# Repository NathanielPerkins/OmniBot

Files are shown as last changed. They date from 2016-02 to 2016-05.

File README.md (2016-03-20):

# OmniBot
EESS Modular Robotics Platform
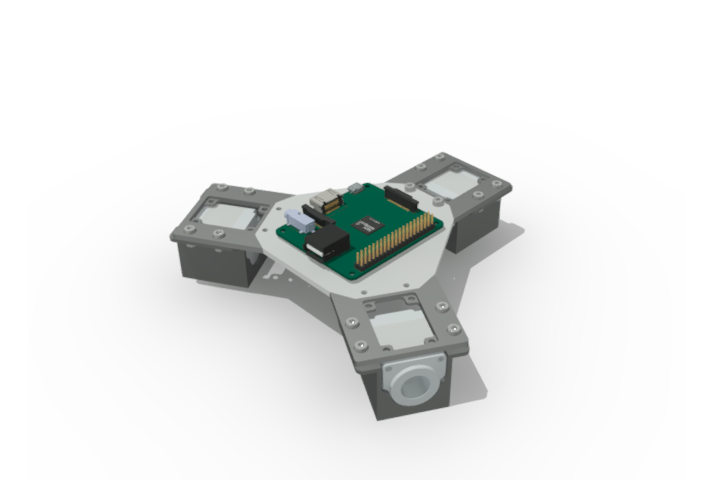
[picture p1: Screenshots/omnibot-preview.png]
OmniBot Render


An open source modular robotics platform designed with KiCAD and FreeCAD.
Custom designed Chassis designed to be laser cut/3d printed/CnC Milled. Custom fit stepper motor mounts with embedded motor controller PCB.

Main Processor unit consists of a Raspberry Pi A+ for path planning and general computation. An STM32 ARM microcontroller system controller will handle the stepper motor control via communication with the RPi A+ board and motor controllers. 

1: System Controller

Requirements: The Electronics design require the following footprint libraries for KiCAD

https://github.com/NathanielPerkins/NPFootprints.pretty
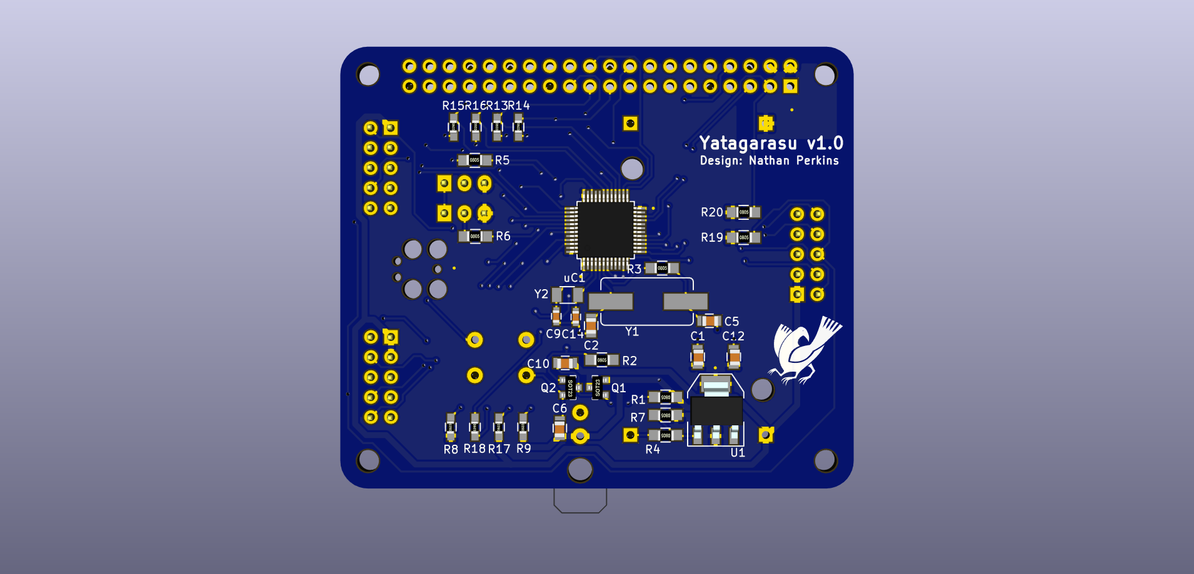
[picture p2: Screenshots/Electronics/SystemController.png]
System Controller


2: Mechanical

Chassis design for overall OmniBot frame, and motor mount system

3: Motor Controller

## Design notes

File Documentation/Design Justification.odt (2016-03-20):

# OmniBot Design Justification

## Electrical

### Component Selection

### Decoupling

All decoupling capacitors are the standard values given in the STM32F10xx hardware design document.

### Programming/Debugging

Pin-outs were selected for the SWD interface based on the STLink/V2 and third party Tag-Connect connector and cable.

### Boot Mode

Jumpers to select boot mode were selected due to cost and simplicity of use. 10K Resistors were selected from the STM32F10xx Hardware Design datasheet recommendations. BOOT0 has no further functionality, however BOOT1 can be used as a general I/O.

### External Power Controller

Design was based off similar purpose IC chips linked below, capacitor (1nF) was estimated based on IC chip solutions.

http://www.vishay.com/docs/73449/si1869dh.pdf

http://www.onsemi.com/pub_link/Collateral/AND9093-D.PDF

### Crystal

Crystal capacitance values were calculated using formulae derived from the following links.

Stray capacitance, from the STM32F103CBT6 datasheet lists the pin capacitance as 5pF. A further 2pF was estimated due to track considerations and a 20pF crystal was used for calculations regarding the High Speed External Clock.

http://www.seeedstudio.com/depot/images/opl/datasheet/306010033.pdf

http://ww1.microchip.com/downloads/en/AppNotes/00826a.pdf

Rs = 910ohms was calculated with the following link

http://www.crystek.com/documents/appnotes/Pierce-GateIntroduction.pdf

### USB

USB 2.0 High speed was selected over USB OTG primarily due to added cost of OTG with no added benefit for current application.

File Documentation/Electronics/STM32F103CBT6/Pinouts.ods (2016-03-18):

Pin | Name | Type | Features |  |  | After Reset | Alternate (default) |  |  |  |  | Alternate (Remap) |  |  | 5V Tolerant | Notes
1 | V_Bat | S |  |  |  |  |  |  |  |  |  |  |  |  | No
2 | PC13-Tamper-RTC | I/O |  |  |  | PC13 | Tamper-RTC |  |  |  |  |  |  |  | No
3 | PC14-OSC32_IN | I/O | Clock |  |  | PC14 | OSC32_IN |  |  |  |  |  |  |  | No
4 | PC15-OSC32_OUT | I/O | Clock |  |  | PC15 | OSC32_OUT |  |  |  |  |  |  |  | No
5 | OSC_IN | I | Clock |  |  | OSC_IN |  |  |  |  |  | PD0 |  |  | No | PD0 output only in 50mHz mode
6 | OSC_OUT | O | Clock |  |  | OSC_OUT |  |  |  |  |  | PD1 |  |  | No | PD1 output only in 50mHz mode
7 | NRST | I/O | JTAG |  |  | NRST |  |  |  |  |  |  |  |  | No
8 | V_SSA | S |  |  |  | V_SSA |  |  |  |  |  |  |  |  | No
9 | V_DDA | S |  |  |  | V_DDA |  |  |  |  |  |  |  |  | No
10 | PA0-WKUP | I/O | Communication | ADC | Timer | PA0 | USART2_CTS | ADC12_IN0 | TIM2_CH1_ETR |  | Wakeup |  |  |  | No
11 | PA1 | I/O | Communication | ADC | Timer | PA1 | USART2_RTS | ADC12_IN1 | TIM2_CH2 |  |  |  |  |  | No
12 | PA2 | I/O | Communication | ADC | Timer | PA2 | USART2_TX | ADC12_IN2 | TIM2_CH3 |  |  |  |  |  | No
13 | PA3 | I/O | Communication | ADC | Timer | PA3 | USART2_RX | ADC12_IN3 | TIM2_CH4 |  |  |  |  |  | No
14 | PA4 | I/O | Communication | ADC |  | PA4 | USART2_CK | ADC12_IN4 |  |  | SPI1_NSS |  |  |  | No
15 | PA5 | I/O | Communication | ADC |  | PA5 |  | ADC12_IN5 |  |  | SPI1_SCK |  |  |  | No
16 | PA6 | I/O | Communication | ADC | Timer | PA6 |  | ADC12_IN6 | TIM3_CH1 |  | SPI1_MISO |  | TIM1_BKIN |  | No
17 | PA7 | I/O | Communication | ADC | Timer | PA7 |  | ADC12_IN7 | TIM3_CH2 |  | SPI1_MOSI |  | TIM1_CH1 |  | No
18 | PB0 | I/O | Communication | ADC | Timer | PB0 |  | ADC12_IN8 | TIM3_CH3 |  |  |  | TIM1_CH2 |  | No
19 | PB1 | I/O | Communication | ADC | Timer | PB1 |  | ADC12_IN9 | TIM3_CH4 |  |  |  | TIM1_CH3 |  | No
20 | PB2 | I/O |  |  |  | PB2/BOOT1 |  |  |  |  |  |  |  |  | Yes
21 | PB10 | I/O | Communication |  | Timer | PB10 | USART3_TX |  |  | I2C2_SCL |  |  | TIM2_CH3 |  | Yes
22 | PB11 | I/O | Communication |  | Timer | PB11 | USART3_RX |  |  | I2C2_SDA |  |  | TIM2_CH4 |  | Yes
23 | V_SS1 | S |  |  |  | V_SS1 |  |  |  |  |  |  |  |  | No
24 | V_DD1 | S |  |  |  | V_DD1 |  |  |  |  |  |  |  |  | No
25 | PB12 | I/O | Communication |  | Timer | PB12 | USART3_CK |  | TIM1_BKIN |  | SPI2_NSS |  |  |  | Yes
26 | PB13 | I/O | Communication |  | Timer | PB13 | USART3_CTS |  | TIM1_CH1N |  | SPI2_SCK |  |  |  | Yes
27 | PB14 | I/O | Communication |  | Timer | PB14 | USART3_RTS |  | TIM1_CH2N |  | SPI2_MISO |  |  |  | Yes
28 | PB15 | I/O | Communication |  | Timer | PB15 |  |  | TIM1_CH3N |  | SPI2_MOSI |  |  |  | Yes
29 | PA8 | I/O | Communication |  | Timer | PA8 | USART1_CK |  | TIM1_CH1 |  | MCO |  |  |  | Yes
30 | PA9 | I/O | Communication |  | Timer | PA9 | USART1_TX |  | TIM1_CH2 |  |  |  |  |  | Yes
31 | PA10 | I/O | Communication |  | Timer | PA10 | USART1_RX |  | TIM1_CH3 |  |  |  |  |  | Yes
32 | PA11 | I/O | Communication |  | Timer | PA11 | USART1_CTS |  | TIM1_CH4 | CANRX | USBDM |  |  |  | Yes
33 | PA12 | I/O | Communication |  | Timer | PA12 | USART1_RTS |  | TIM1_ETR | CANTX | USBDP |  |  |  | Yes
34 | PA13 | I/O | JTAG |  |  | JTMS |  |  |  |  |  | PA13 |  |  | Yes
35 | V_SS2 | S |  |  |  | V_SS2 |  |  |  |  |  |  |  |  | No
36 | V_DD2 | S |  |  |  | V_DD2 |  |  |  |  |  |  |  |  | No
37 | PA14 | I/O | JTAG |  |  | JTCK |  |  |  |  |  | PA14 |  |  | Yes
38 | PA15 | I/O | JTAG |  | Timer | JTDI |  |  |  |  |  | PA15 | TIM2_CH1_ETR | SPI1_NSS | Yes
39 | PB3 | I/O | JTAG |  | Timer | JTDO |  |  |  |  |  | PB3 | TIM2_CH2 | SPI1_CLK | Yes
40 | PB4 | I/O | JTAG |  |  | JNTRST |  |  |  |  |  | PB4 | TIM3_CH1 | SPI1_MISO | Yes
41 | PB5 | I/O | Communication |  | Timer | PB5 |  |  |  | I2C1_SMBA |  |  | TIM3_CH2 | SPI1_MOSI | No
42 | PB6 | I/O | Communication |  | Timer | PB6 |  |  | TIM4_CH1 | I2C1_SCL |  |  |  | USART1_TX | Yes
43 | PB7 | I/O | Communication |  | Timer | PB7 |  |  | TIM4_CH2 | I2C1_SDA |  |  |  | USART1_RX | Yes
44 | BOOT0 | I |  |  |  | BOOT0 |  |  |  |  |  |  |  |  | No
45 | PB8 | I/O | Communication |  | Timer | PB8 |  |  | TIM4_CH3 |  |  |  | CANRX | I2C1_SCL | Yes
46 | PB9 | I/O | Communication |  | Timer | PB9 |  |  | TIM4_CH4 |  |  |  | CANTX | I2C1_SDA | Yes
47 | V_SS3 | S |  |  |  | V_SS3 |  |  |  |  |  |  |  |  | No
48 | V_DD3 | S |  |  |  | V_DD3 |  |  |  |  |  |  |  |  | No

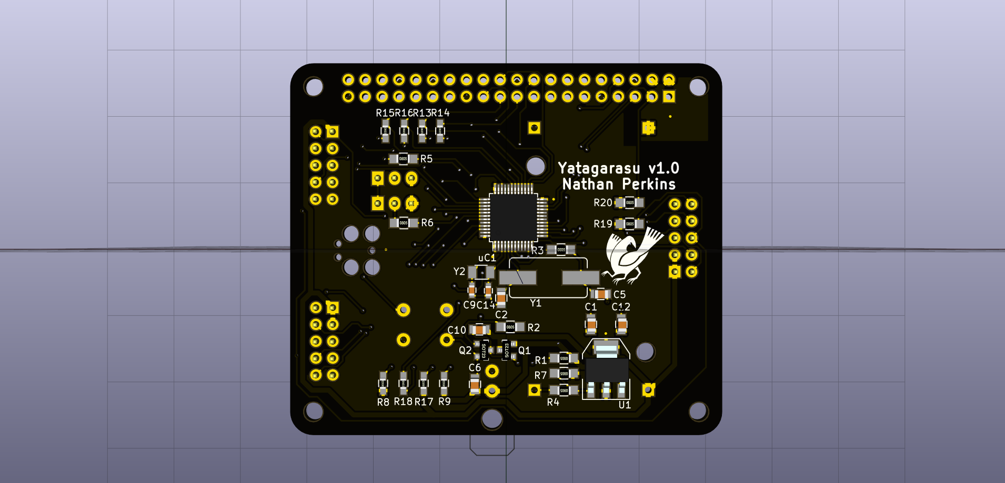
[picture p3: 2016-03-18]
Electronics/System Controller/SystemController.png

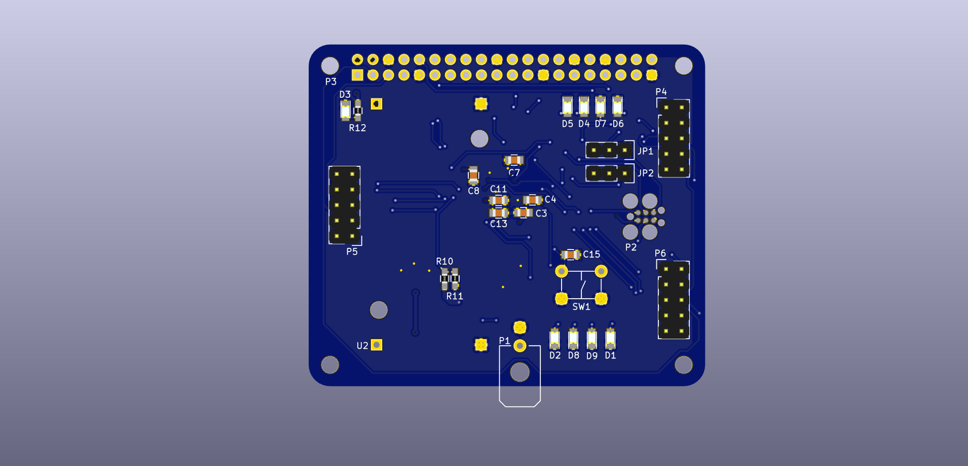
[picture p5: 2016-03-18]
Screenshots/Electronics/SCTop.png

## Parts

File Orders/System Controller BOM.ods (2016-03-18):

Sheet: Sheet1
Item | Designator | Package Type | RS-Stock # | Amount | Price | Zelda
STM32F103CBT6 | uC1 |  | 402-273 | 3 |  | http://au.rs-online.com/web/p/microcontrollers/0402273/?searchTerm=stm32f103cbt6
R 10K | R1,2,5,6 |  | 223-0562 | 1 pack |  | http://au.rs-online.com/web/p/surface-mount-fixed-resistors/2230562/
Q NPN 2N7002 | Q1 |  | 436-7379 | 1 pack |  | http://au.rs-online.com/web/p/mosfet-transistors/4367379/
Q PNP Si2343CDS | Q2 |  | 812-3120 | 1 pack |  | http://au.rs-online.com/web/p/mosfet-transistors/8123120/?searchTerm=SI2343CDS-T1-GE3
C 1nF | C10 |  | 264-4337 | 1 pack |  | http://au.rs-online.com/web/p/ceramic-multilayer-capacitors/2644337/
C 22pF | C2,5 |  | 264-4258 | 1 pack |  | http://au.rs-online.com/web/p/ceramic-multilayer-capacitors/2644258/
R 910R | R3 |  | 662-0922 | 1 pack |  | http://au.rs-online.com/web/p/surface-mount-fixed-resistors/6620922/
C 4.7pF | C9,14 |  | 148-014 | 1 pack |  | http://au.rs-online.com/web/p/ceramic-multilayer-capacitors/0148014/
C 100nF | C1,3,4,7,11,15 |  | 264-4416 | 1 pack |  | http://au.rs-online.com/web/p/ceramic-multilayer-capacitors/2644416/
C 1uF | C13,12,6 |  | 451-5770 | 1 pack |  | http://au.rs-online.com/web/p/ceramic-multilayer-capacitors/4515770/
Push Button Switch | SW1 |  | DHT-1152 | 1 pack |  | http://www.seeedstudio.com/depot/OPLopen-parts-library-catalog-c-136_138/?ref=side
Y 8MHz | Y1 |  | 5032/4P | 1 pack |  | as above
Y32kHz | Y2 |  | FC-135 | 1 pack |  | as above
D LEDs | D1,2,3,4,5,6,7,8,9 |  | 497-4804 | 1 pack |  | http://au.rs-online.com/web/p/visible-leds/6545391/
R 68R | R8,13,14,15,16,18 |  | 223-0275 | 1 pack |  | http://au.rs-online.com/web/p/surface-mount-fixed-resistors/2230275/
2x20 Female Headers | P3 |  | 681-6851 | 5 |  | http://au.rs-online.com/web/p/pcb-sockets/6816851/
5v Buck Module | U2 |  | 106990003 | 3 |  | http://www.seeedstudio.com/depot/Adjustable-DCDC-Power-Converter-125V-35V3A-p-1534.html
R 560R | R9, 17 |  | 223-0382 | 1 pack |  | http://au.rs-online.com/web/p/surface-mount-fixed-resistors/2230382/
Q LM317 | U1 | X | 533-5705 | 3 |  | http://au.rs-online.com/web/p/linear-voltage-regulators/5335705/
R 150R | R12 |  | 223-0310 | 1 pack |  | http://au.rs-online.com/web/p/surface-mount-fixed-resistors/2230310/
R 390R | R4 |  | 223-0360 | 1 pack |  | http://au.rs-online.com/web/p/surface-mount-fixed-resistors/2230360/
R 240R | R7 |  | 679-1125 | 1 pack |  | http://au.rs-online.com/web/p/surface-mount-fixed-resistors/6791125/
P Amphenol T821 | P4,5,6 |  | 832-3528 | 10 |  | http://au.rs-online.com/web/p/pcb-headers/8323528/
C 10uF | C8 |  | 691-1161 | 1 pack |  | http://au.rs-online.com/web/p/ceramic-multilayer-capacitors/6911161/
Molex Femal Wire-Board Connector |  |  | 233-2747 | 5 units |  | http://au.rs-online.com/web/p/pcb-connector-housings/2332747/
Molex Male Board-Wire Connector | P1 |  | 233-2933 | 5 units |  | http://au.rs-online.com/web/p/pcb-headers/2332933/
Molex Cable Connectors |  |  | 832-3617 | 12 |  | http://au.rs-online.com/web/p/idc-connectors/8323617/?searchTerm=T812110A100CEU

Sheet: Sheet2
Item | Designator | Package Type | RS-Stock # | Amount required | Final Price | Zelda
C 100uF |  | Al 6.3x7.7 | 739-3056 | 5 | 1.04 | http://au.rs-online.com/web/p/aluminium-capacitors/7393056/
C 100nF |  | 0603 | 264-4646 | 10 | 0.1 | http://au.rs-online.com/web/p/ceramic-multilayer-capacitors/2644646/
C 10nF |  | 0603 | 476-5997 | 5 | 0.11 | http://au.rs-online.com/web/p/ceramic-multilayer-capacitors/4765997/
C 0.47uF |  | 0805 | 147-998 | 5 | 1.3 | http://au.rs-online.com/web/p/ceramic-multilayer-capacitors/0147998/
Rtrim 50K |  | unknown SMD | 691-7103 | 5 | 2.92 | http://au.rs-online.com/web/p/trimmer-resistors/6917103/
R 1M |  | 0805 | 223-0821 | 5 | 1.95 | http://au.rs-online.com/web/p/surface-mount-fixed-resistors/2230821/
R 30K |  | 0603 | 679-0197 | 5 | 1.2 | http://au.rs-online.com/web/p/surface-mount-fixed-resistors/6790197/
R 100m |  | 1206 | 721-5710 | 10 | 4.9 | http://au.rs-online.com/web/p/surface-mount-fixed-resistors/7215710/
R 10K |  | 0805 | 740-9072 | 5 | 1.5 | http://au.rs-online.com/web/p/surface-mount-fixed-resistors/7409072/
U DRV8825 |  | HTSSOP | 742-2873 | 5 | 46.65 | http://au.rs-online.com/web/p/motor-driver-ics/7422873

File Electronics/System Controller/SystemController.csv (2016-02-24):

Reference | Value | Footprint | Datasheet
uC1 | STM32F103CBT6 | Housings_QFP:LQFP-48_7x7mm_Pitch0.5mm
P1 | Battery Input | Pin_Headers:Pin_Header_Straight_1x02
JP1 | BOOT0 | Pin_Headers:Pin_Header_Straight_1x03
JP2 | BOOT1 | Pin_Headers:Pin_Header_Straight_1x03
R6 | 10K | Resistors_SMD:R_0805_HandSoldering
R5 | 10K | Resistors_SMD:R_0805_HandSoldering
Q1 | 2N7002 | TO_SOT_Packages_SMD:SOT-23
R2 | 10K | Resistors_SMD:R_0805_HandSoldering
R1 | 10K | Resistors_SMD:R_0805_HandSoldering
Q2 | Si2343CDS | TO_SOT_Packages_SMD:SOT-23
C10 | 1nF | Capacitors_SMD:C_0805
R20 | R_I2C | Resistors_SMD:R_0805_HandSoldering
R19 | R_I2C | Resistors_SMD:R_0805_HandSoldering
Y1 | 8MHz | NPFootprints:Seeedstudio-8MHzCrystal
C2 | 22pF | Capacitors_SMD:C_0805
C5 | 22pF | Capacitors_SMD:C_0805
R3 | 910 | Resistors_SMD:R_0805_HandSoldering
Y2 | 32kHz | NPFootprints:Seeedstudio-32kHz_Crystal-FC135
C9 | 4.7pF | Capacitors_SMD:C_0603
C14 | 4.7pF | Capacitors_SMD:C_0603
C1 | 100nF | Capacitors_SMD:C_0805
C8 | 10uF | Capacitors_SMD:C_0805
C3 | 100nF | Capacitors_SMD:C_0805
C4 | 100nF | Capacitors_SMD:C_0805
C7 | 100nF | Capacitors_SMD:C_0805
C11 | 100nF | Capacitors_SMD:C_0805
C13 | 1uF | Capacitors_SMD:C_0805
C15 | 100nF | Capacitors_SMD:C_0805
SW1 | SW_PUSH | NPFootprints:Seeedstudio-Pushbutton-DHT-1152
P2 | SWD | NPFootprints:Tag-Connect_6P_Leads
D1 | LED | LEDs:LED_0805
R8 | 68 | Resistors_SMD:R_0603_HandSoldering
D2 | LED | LEDs:LED_0805
R9 | 560 | Resistors_SMD:R_0603_HandSoldering
D3 | LED | LEDs:LED_0805
R12 | 150 | Resistors_SMD:R_0603_HandSoldering
D4 | LED | LEDs:LED_0805
R13 | 68 | Resistors_SMD:R_0603_HandSoldering
D5 | LED | LEDs:LED_0805
R14 | 68 | Resistors_SMD:R_0603_HandSoldering
D6 | LED | LEDs:LED_0805
R15 | 68 | Resistors_SMD:R_0603_HandSoldering
R16 | 68 | Resistors_SMD:R_0603_HandSoldering
R10 | R | Resistors_SMD:R_0603_HandSoldering
R11 | R | Resistors_SMD:R_0603_HandSoldering
P3 | Raspberry Pi A+ Connectors | NPFootprints:Raspberry_Pi_A+
U2 | Seeedstudio_Buck_5v | NPFootprints:Seeedstudio_5V_Buck
D8 | LED | LEDs:LED_0805
R17 | 560 | Resistors_SMD:R_0603_HandSoldering
P4 | Harwin-10P | NPFootprints:Conn-Harwin-10p
P5 | Harwin-10P | NPFootprints:Conn-Harwin-10p
P6 | Harwin-10P | NPFootprints:Conn-Harwin-10p
D9 | LED | LEDs:LED_0805
R18 | 68 | Resistors_SMD:R_0603_HandSoldering
D7 | LED | LEDs:LED_0805
R4 | 390 | Resistors_SMD:R_0805_HandSoldering
U1 | LM317 | TO_SOT_Packages_SMD:SOT-223
R7 | 240 | Resistors_SMD:R_0805_HandSoldering
C12 | 1uF | Capacitors_SMD:C_0805
C6 | 1uF | Capacitors_SMD:C_0805

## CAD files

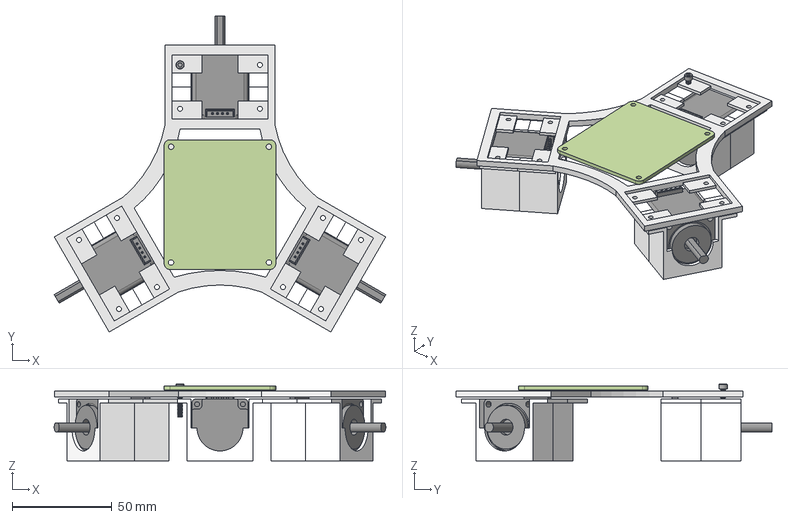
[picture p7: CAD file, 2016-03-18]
Mechanical/eess.omnibot.beta.fcstd
166.2 x 158.3 x 38.5 mm
MotorMount.Back.Out
MotorMount.Back.In
Stepper.Back
M2.5x16
MotorMount.Left.In
MotorMount.Left.Out
Stepper.Left
MotorMount.Right.Out
MotorMount.Right.In
Stepper.Right
A+.Placeholder
PolarPattern

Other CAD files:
Electronics/System Controller/3D/SystemController.fcstd

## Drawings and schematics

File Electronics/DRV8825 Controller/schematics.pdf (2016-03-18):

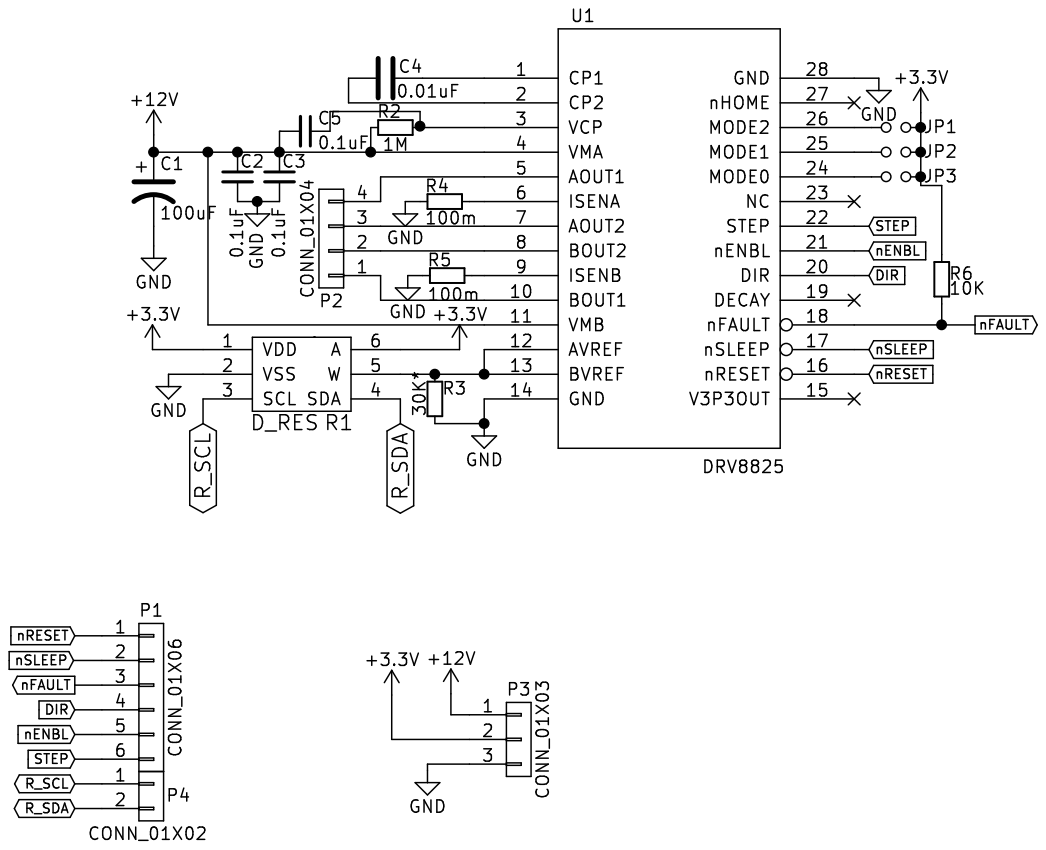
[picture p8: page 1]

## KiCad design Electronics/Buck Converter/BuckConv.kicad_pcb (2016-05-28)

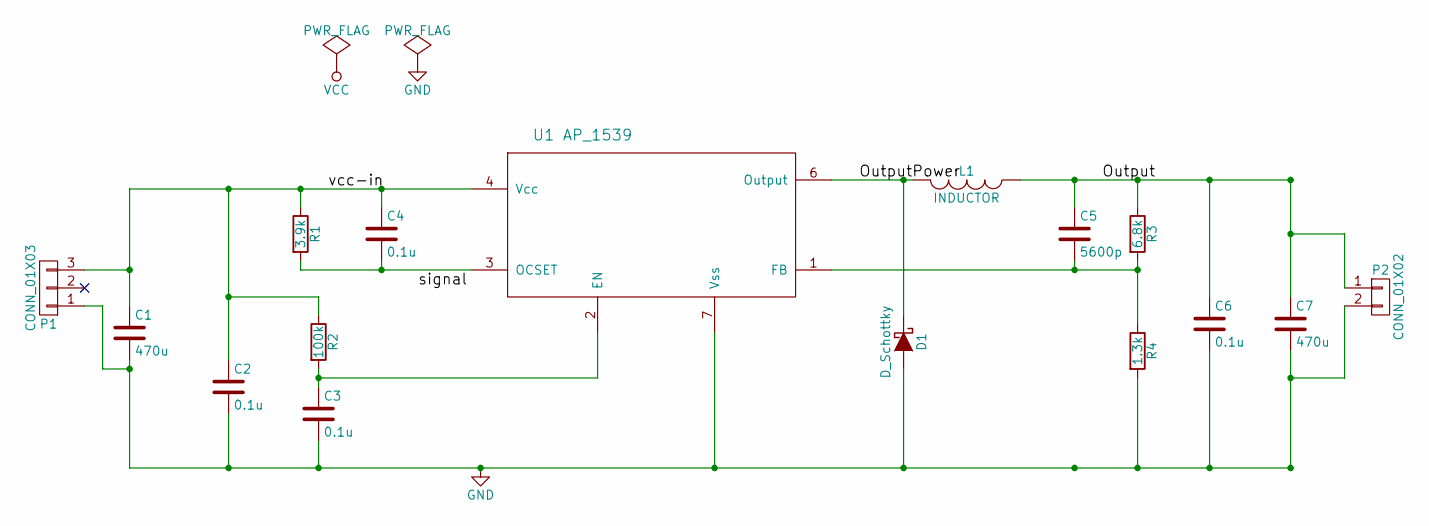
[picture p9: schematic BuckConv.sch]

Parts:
C1: 470u; c_elec_8x10
C2, C3, C4, C6: 0.1u; C_0805_HandSoldering
C5: 5600p; C_1206_HandSoldering
C7: 470u; c_elec_8x10.5
D1: D_Schottky; SOD-123
L1: INDUCTOR; Inductor1
P1: CONN_01X03; Pin_Header_Straight_1x03
P2: CONN_01X02; Socket_Strip_Straight_1x02
R1: 3.9k; R_0805_HandSoldering
R2: 100k; R_0805_HandSoldering
R3: 6.8k; R_0805_HandSoldering
R4: 1.3k; R_0805_HandSoldering
U1: AP_1539; BuckConv

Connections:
/Output: C5.1, C6.1, C7.1, L1.1, P2.1, R3.1
/OutputPower: D1.1 (K), L1.2, U1.6 (Output)
/vcc-in: C1.1, C2.1, C4.1, P1.3, R1.1, R2.1, U1.4 (Vcc)
GND: C1.2, C2.2, C3.2, C6.2, C7.2, D1.2 (A), P1.1, P2.2, R4.2, U1.7 (Vss)
unnamed: C3.1, R2.2, U1.2 (EN)
unnamed: C4.2, R1.2, U1.3 (OCSET)
unnamed: C5.2, R3.2, R4.1, U1.1 (FB)

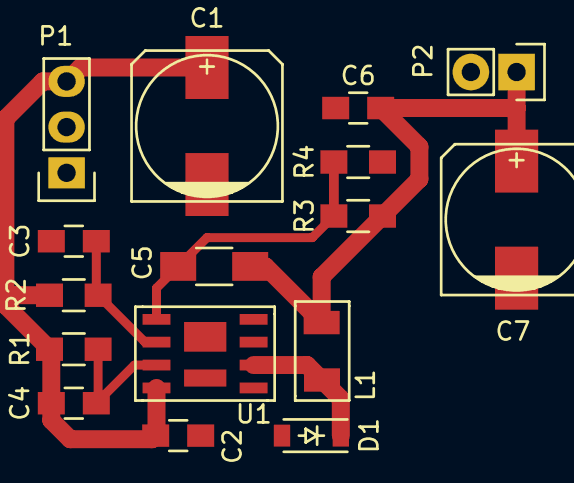
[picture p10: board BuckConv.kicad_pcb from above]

Board: 2 copper layers, 16 parts (0 on the bottom side), 7 nets.

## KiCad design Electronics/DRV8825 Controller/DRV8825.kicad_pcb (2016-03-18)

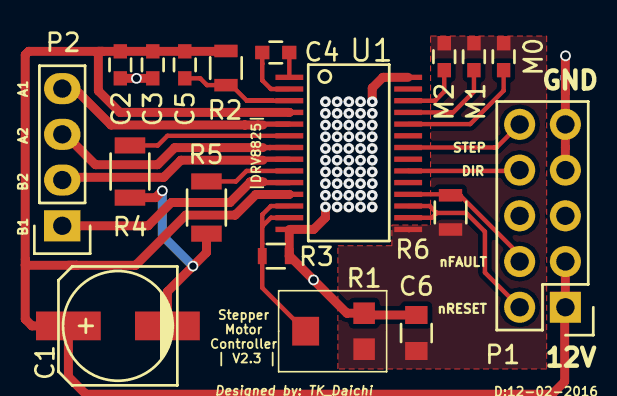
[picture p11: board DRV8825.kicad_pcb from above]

Board: 2 copper layers, 18 parts (0 on the bottom side), 20 nets.

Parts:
C1: 100uF; c_elec_6.3x7.7
C2, C3, C5: 0.1uF; C_0603
C4: 0.01uF; C_0603
C6: 0.47uF; C_0805
M0, M1, M2: Jumper_NO_Small; C_0603
P1: CONN_01X10; Pin_Header_Straight_2x05
P2: CONN_01X04; Pin_Header_Straight_1x04
R1: 50K Pot; Potentiometer
R2: 1M; R_0805
R3: 30K*; R_0603
R4, R5: 100m; R_1206
R6: 10K; R_0805
U1: DRV8825; DRV-8825_FOOTPRINT

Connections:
+3V3: C6.1, M0.2, M1.2, M2.2, R1.1, R6.1, U1.15
+12V: C1.1, C2.1, C3.1, C5.2, P1.1, P1.3, R2.2, U1.4, U1.11
DIR: P1.8, U1.20
GND: C1.2, C2.2, C3.2, C6.2, P1.7, P1.9, R1.3, R3.2, R4.2, R5.2, U1.14, U1.28
unnamed: C4.1, U1.2
unnamed: C4.2, U1.1
unnamed: C5.1, R2.1, U1.3
unnamed: M2.1, U1.26
unnamed: M1.1, U1.25
unnamed: M0.1, U1.24
unnamed: P2.1, U1.10
unnamed: P2.2, U1.8
unnamed: P2.3, U1.7
unnamed: P2.4, U1.5
unnamed: R1.2, R3.1, U1.12, U1.13
unnamed: R4.1, U1.6
unnamed: R5.1, U1.9
STEP: P1.10, U1.22
nFAULT: P1.4, R6.2, U1.18
nRESET: P1.2, U1.16, U1.17

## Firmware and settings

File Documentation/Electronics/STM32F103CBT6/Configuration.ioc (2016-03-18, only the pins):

Mcu.UserName=STM32F103CBTx
PA10.Signal=USART1_RX
PA11.Signal=USB_DM
PA12.Signal=USB_DP
PA13.Signal=SYS_JTMS-SWDIO
PA14.Signal=SYS_JTCK-SWCLK
PA15.Signal=GPIO_Output
PA2.Signal=GPIO_Input
PA3.Signal=GPIO_Input
PA4.Signal=GPIO_Input
PA5.Signal=ADCx_IN5
PA6.Signal=S_TIM3_CH1
PA7.Signal=S_TIM3_CH2
PA8.Signal=USART1_CK
PA9.Signal=USART1_TX
PB0.Signal=S_TIM3_CH3
PB10.Signal=I2C2_SCL
PB11.Signal=I2C2_SDA
PB12.Signal=SPI2_NSS
PB13.Signal=SPI2_SCK
PB14.Signal=SPI2_MISO
PB15.Signal=SPI2_MOSI
PB3.Signal=SYS_JTDO-TRACESWO
PB4.Signal=GPIO_Output
PB5.Signal=GPIO_Output
PB6.Signal=GPIO_Output
PB7.Signal=GPIO_Output
PB8.Signal=GPIO_Output
PC14-OSC32_IN.Signal=RCC_OSC32_IN
PC15-OSC32_OUT.Signal=RCC_OSC32_OUT
PD0-OSC_IN.Signal=RCC_OSC_IN
PD1-OSC_OUT.Signal=RCC_OSC_OUT

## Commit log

2016-02-24 Initial Commit of backlog
    [SystemController-B.Adhes.gbr, SystemController-B.Cu.gbr, SystemController-B.Mask.gbr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]
2016-03-18 Refactoring local repository.
    [Pinouts.ods, SystemController.kicad_pcb, SystemController.sch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]
2016-03-18 Re-organizing repo
    [SystemController-B.Adhes.gbr, SystemController-B.Cu.gbr, SystemController-B.Mask.gbr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]
2016-03-18 Adding BOM
    [System Controller BOM.ods]
2016-03-18 Umm 1.0
    Pushed?
    [DRV8825-B.Adhes.gbr, DRV8825-B.Cu.gbr, DRV8825-B.Mask.gbr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]
2016-03-18 Revert "Umm 1.0"
    This reverts commit cc9c9a6458a31b3baf7c23216ac2a969229ed4a6.
    [DRV8825-B.Adhes.gbr, DRV8825-B.Cu.gbr, DRV8825-B.Mask.gbr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]
2016-03-18 I did something
    [DRV8825-B.Adhes.gbr, DRV8825-B.Cu.gbr, DRV8825-B.Mask.gbr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]
2016-03-19 PCB Tidy-up
    Slight changes to SystemController PCB
    [SystemController.kicad_pcb, SystemController.sch]
2016-03-20 WIP: System-Controller Power Redesign
    [SystemController.kicad_pcb, SystemController.sch]
2016-05-28 Create Buck Converter
2016-05-28 Buck Converter addition
    Addition of the buck converter prototype design to be later implemented into the final module. Using the AP1539 chip.
    [BuckConv.kicad_pcb, BuckConv.sch]
